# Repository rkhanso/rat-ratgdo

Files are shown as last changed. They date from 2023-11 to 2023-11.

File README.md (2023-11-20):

# My Addition
-an Eagle Schematic and PCB that is proven to work (I'm using it on my Chamberlain garage door).

My schematic/board uses a 2n7000 and a RFP30N06LE.

Controller is a generic ESP8266 D1 Mini.

There is only one 3-pin screw connector. Why do you need anything more? 

No extra dry contacts or anything. Just use this in Home Assistant and you'll be fine.

# rat-ratgdo
RAGE
AGAINST
THE
RATGDO



Credit and inspiration for this work goes to [@rlowens](https://github.com/rlowens) to let me know that there are other technical folks out there who needed this other than myself.

## Overview
This is an open source schematic for the ratgdo, based on the v2.5 [ratgdo](https://github.com/PaulWieland/ratgdo) PCB and code but installed using the [ESPHome fork](ESPHome%20vs%20native%20ratgdo.md) of ratgdo.  We feel there is cognitive dissonance between the refusal to provide (and deleting requests for) schematics for the ratgdo PCB against the ratgdo project's use of open source code, open source licensing, and libraries used by other open source projects, as well as the inception reasoning for the ratgdo project which was to ensure that nobody is at the mercy of a third party that might stop selling the PCBs.

This project was created to allow people who need a ratgdo solution for their garage door opener but either cannot, or choose not to, source the solution from Paul Wieland and be locked into that 3rd party. It also ensures that the PCB can be recreated as and when the project maintainer gives up on the project (much like Chamberlain themselves might do with their MyQ Cloud Service) and stops selling PCBs.

### You are expected to know how to create the described circuit using your own prototyping skills.  That is, this project is for people who can solder well and know how to read schematics

The PCB schematic here does not describe any circuitry other than the serial line garage door control and obstruction sensor.  All other optional features provided by ratgdo could also be reverse engineered as needed.

**If you want to buy a pre-made ratgdo setup, purchase it [from Paul Wieland](https://github.com/PaulWieland/ratgdo).**

PCB Link

See images of a [working breadboard prototype](images/Breadboard_working.png) and the [subsequent soldered prototype using a D1 shield](images/Simple%20prototype%20using%20D1%20shield.jpg).  Both of these prototypes are using 2n7000 MOSFETs exclusively, but that is because they are prototypes and long term reliability of data transmission when using the 2n7000 has not been confirmed.  See the section below on needed components for context.

## Components needed
This schematic assumes the use of through-hole components.  If you wish to use SMD components, please refer to the [FAQ](FAQ.md#what-if-i-want-to-use-sot-23-smd-components).

Aside from the obvious requirement of a [supported ESP-32 or ESP8266 board](Supported%20Boards.md) flashed with the [ESPHome version](https://github.com/ratgdo/esphome-ratgdo), you will need 3x 10 kohm (kilo-ohm) resistors, and two 2n7000 N-channel MOSFET (TO-92 package is easiest).  It is also recommended you aquire a suitable 3-post screw terminal and some red, white, and black wire for connecting to the door opener.  These connections are very low current, so you can get away with fairly thin wire.

**Note:** Our simple through-hole Bill Of Materials uses 2n7000 MOSFETs for both RX and TX, however depending on the manufacturere of your 2n7000 and its production batch, it might not be 100% reliable for the TX circuit.  There are many examples working using the 2n7000 however, so there is a very high chance it will work.

## INSTALL REQUIREMENTS
Due the schematics we have provided and how they are laid out, you must use the ESPHome fork of ratgdo and - for ESP8266 based boards - select the blue v2.5 board on the ESPhome [web installer page](https://ratgdo.github.io/esphome-ratgdo/).  For ESP-32 based boards the above does not currently apply and you must use the v2.0 installer and follow our ESP-32 schematic we provide in the Supported Boards page.

For the ESP8266 based boards, if installing using Paul Wieland's native ratgdo installer and you install for a v2.0 board, you must wire your TX to D4 (GPIO2) rather than D1 (GPIO5).

## Having a PCB printed
You may use the files from the [schematics folder](kicad_files) to have your own PCB printed.  Shown is an example 3D render of an ESP32 based board using a Wemos ESP32 D1 board.

3D render of printed PCB
_An example of the D1 Mini ESP32 Wide Format_

### Schematic options
We provide a few options of schematic files suitable for sending to a PCB printing company.  Currently provided are:
- [Wemos D1 Mini ESP8266](kicad_files/D1%20Mini%20-%20ESP8266)
- [Wemos D1 Mini ESP32](kicad_files/D1%20Mini%20-%20ESP32) (massive overkill for ratgdo but it's your choice!)
- [Wemos D1 Mini ESP32 Wide Format](kicad_files/D1%20Mini%20Wide%20-%20ESP32)
- [Bare ESP8266 module](kicad_files/Bare%20ESP8266)

> If you just want to try ordering a board from somewhere like PCBWay, then check out the most recent [build artifacts](https://github.com/Kaldek/rat-ratgdo/actions/workflows/pcb.yaml)

## How the ratgdo circuit works
The ratgdo circuitry which we cover in this project consists of two sections; Garage Door control and obstruction sensors.

### Garage Door Control
#### Description of the Chamberlain configuration
The Chamberlain garage door control circuit is a two-wire setup consisting of a Ground, and a combined +12v power and serial data line.  The serial data line is held at 12v unless data transmission is occurring.  Data transmission is performed by pulling the 12v line down to GND for each data bit.  The benefit here is that a single wire can be used for providing power to door control panels and data transmssion on a single wire.  The use of appropriately sized capacitors in door control panels means they do not switch off during data transmission.

#### How ratgdo interfaces with the Chamberlain wiring
The ratgdo taps into the red control wire and uses this single wire for transmission of commands onto the serial bus, and for receiving data from the serial bus.  As it is a single wire protocol and operates half-duplex, the ratgdo circuitry uses N-channel MOSFETs wired in a manner which allows the ESP8266 to never transmit when the serial line is already low.

In operation, this means that the ratgdo is mostly listening to the serial bus to ensure it is keeping track of the state of the door.  For example, if the door is manually opened (or opened by use of the MyQ app even), these events are broadcast onto the serial bus by the door controller.  ratgdo is therefore able to know that the state of the door has changed.  In turn, this means that when controlling ratgdo via Home Assistant, the status of the door in HA is always up to date.

#### Wiring to Garage Door


### Obstruction sensor
The ratgdo monitors the real-time state of the obstruction sensors directly.  We assume this is because obstruction status is not broadcast in real time by the door controller, and safety is paramount.  It allows you to set up real-time alerts in Home Assistant for any time the door is obstructed.  The ratgdo taps into the obstruction sensor power wire which also acts as a communication bus, however the signalling is only an ongoing status of whether the obstruction sensors are working and whether there is an obstruction.

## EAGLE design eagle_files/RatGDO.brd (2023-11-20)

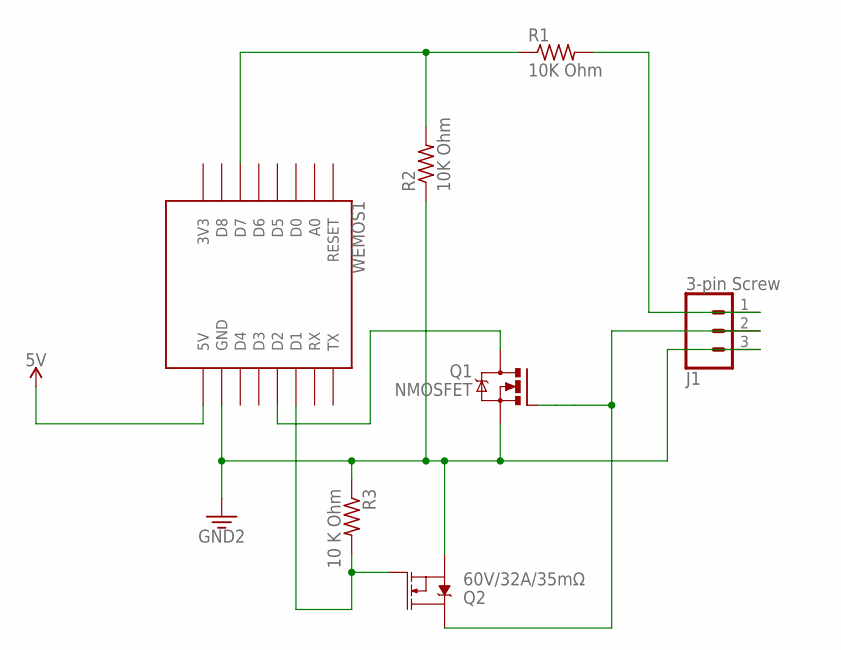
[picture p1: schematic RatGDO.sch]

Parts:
J1: 3-pin Screw; SCREWTERMINAL-3.5MM-3
Q1: NMOSFET; TO92
Q2: 60V/32A/35mΩ; TO220V
R1, R2: 10K Ohm; 0309/12
R3: 10 K Ohm; 0309/12
WEMOS1: WEMOS-D1-MINI

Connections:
5V: WEMOS1.5V
D1: Q2.1 (G), R3.2, WEMOS1.D1
D2: Q1.1 (D), WEMOS1.D2
D7: R1.1, R2.2, WEMOS1.D7
GND: J1.3, Q1.3 (S), Q2.3 (S), R2.1, R3.1, WEMOS1.GND
PIN1: J1.1, R1.2
PIN2: J1.2, Q1.2 (G), Q2.2 (D)

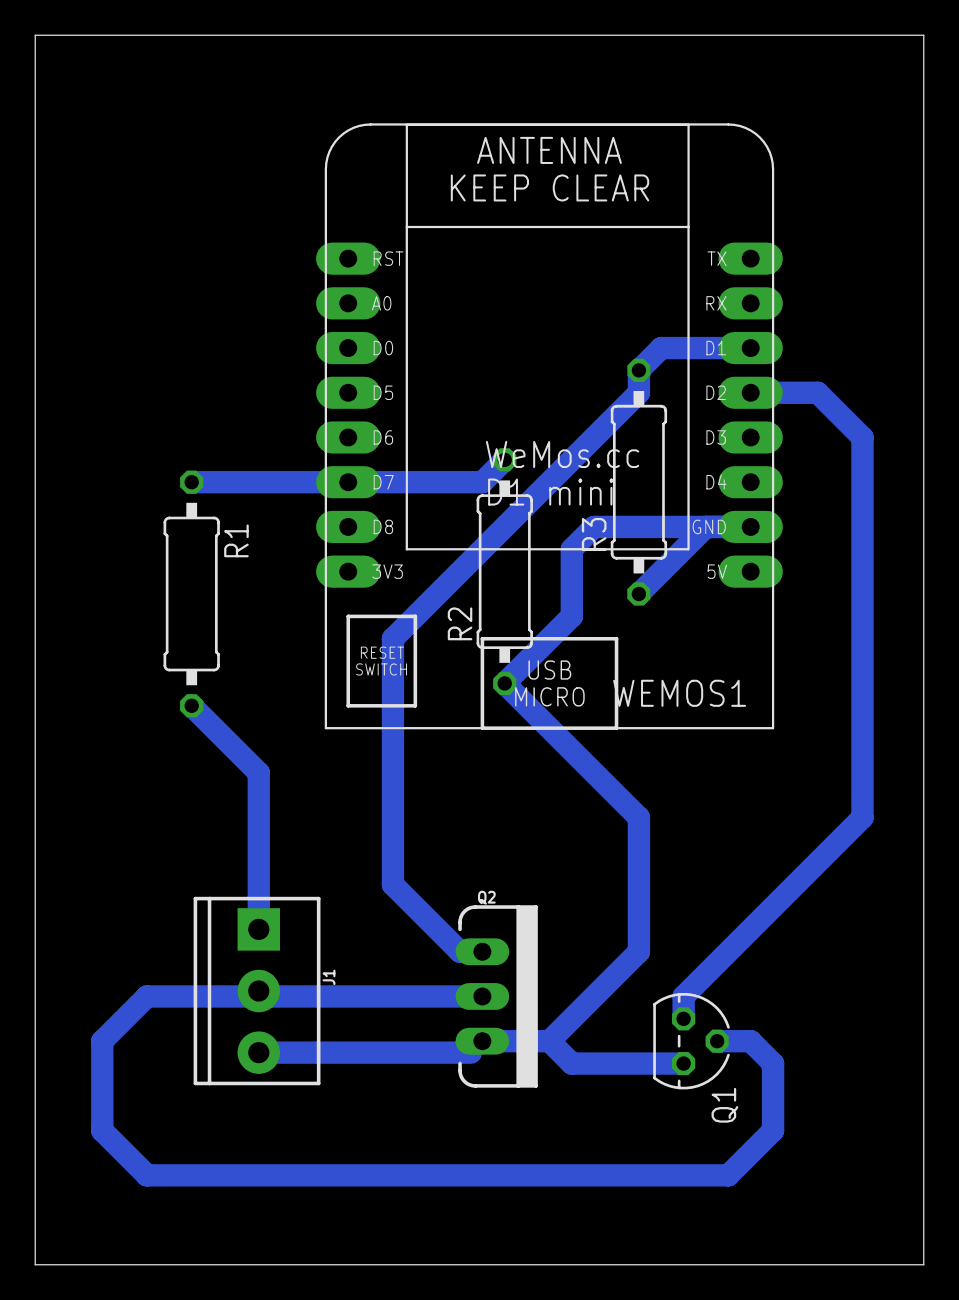
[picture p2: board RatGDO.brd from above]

Board: 2 copper layers, 50.5 x 69.8 mm, 7 parts (0 on the bottom side), 6 nets.

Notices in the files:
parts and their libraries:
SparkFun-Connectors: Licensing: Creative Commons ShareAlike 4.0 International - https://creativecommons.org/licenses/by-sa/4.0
